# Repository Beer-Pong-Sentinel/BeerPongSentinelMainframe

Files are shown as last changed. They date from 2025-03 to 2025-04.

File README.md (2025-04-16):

# Beer Pong Sentinel Project
This page contains a detailed description of the Beer Pong Sentinel project for the Engineering Physics capstone course at UBC.

## Our Team

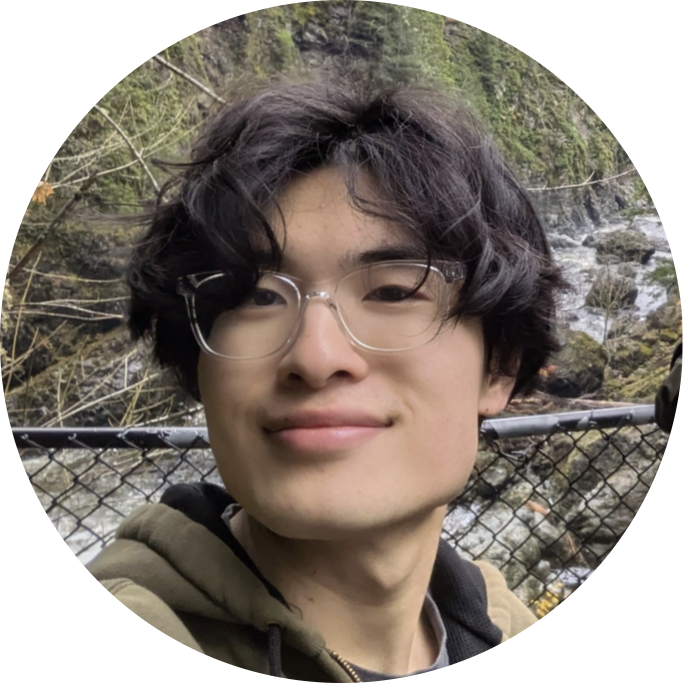
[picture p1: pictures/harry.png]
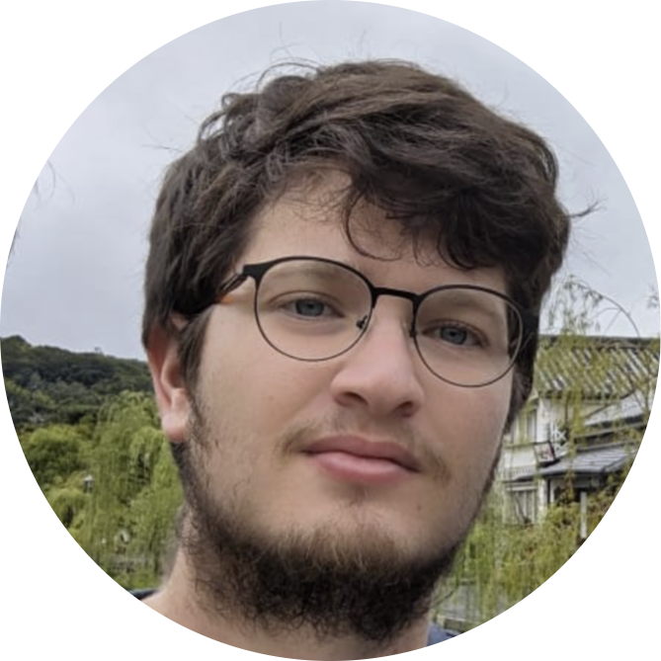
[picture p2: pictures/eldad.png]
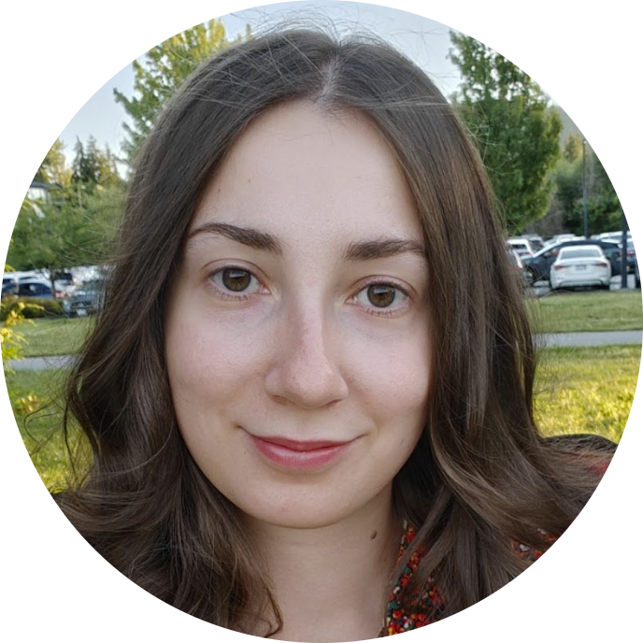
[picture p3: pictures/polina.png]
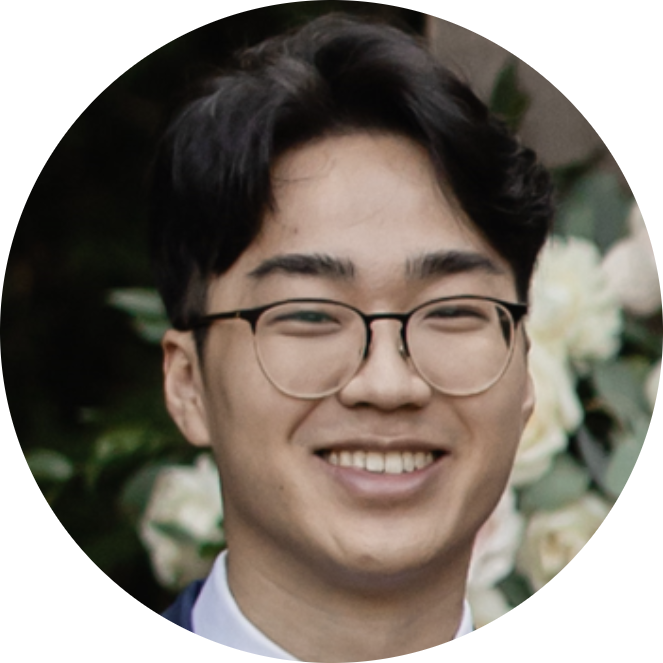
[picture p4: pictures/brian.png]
|  |  |  |  |
|:---:|:---:|:---:|:---:|
| **Harry Hu** | **Eldad Zipori** | **Polina Shopina** | **Brian Yan** |
| [LinkedIn](https://www.linkedin.com/in/harrytyhu/) | [LinkedIn](https://www.linkedin.com/in/eldad-zipori-a411a5157/) | [LinkedIn](https://www.linkedin.com/in/polina-shopina/) | [LinkedIn](https://www.linkedin.com/in/brian-yan/) |

## Background
The inspiration for this project came from an innocent university game - beer pong.
We thought, “it would be pretty cool to build a robot that could intercept all of our opponent's shots”! 

Although we've pivoted away from ping pong balls to the larger and more predictable tennis balls, our goal remains the same: to prevent a target from reaching a zone at the edge of a table using an interception system.

### General Interception Process
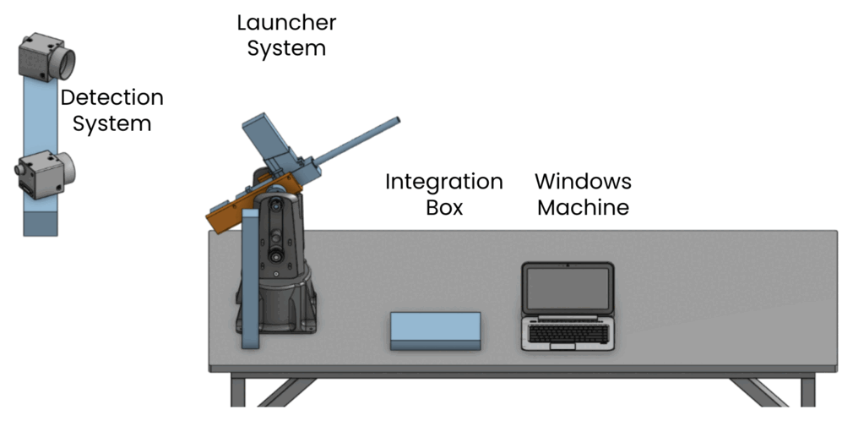
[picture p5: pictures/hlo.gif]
High Level Overview


The small animation shows the different high level stages our system has to take to intercept a ball.

First you see the general setup of our system, and it's different components. The remaining steps are as follows:
* our cameras detect a tennis ball in the air and triangulate its 3D location
* our cameras continue capturing frames until we have enough data to predict the target's trajectory
* we compute the predicted trajectory and based on our understanding of system latency, determine where along the trajectory to intercept the target
* we rotate our launcher in the altitude and azimuth directions
* we trigger the launcher to fire an interceptor at the right time

### Error, Latency, Jitter, and Uncertainty

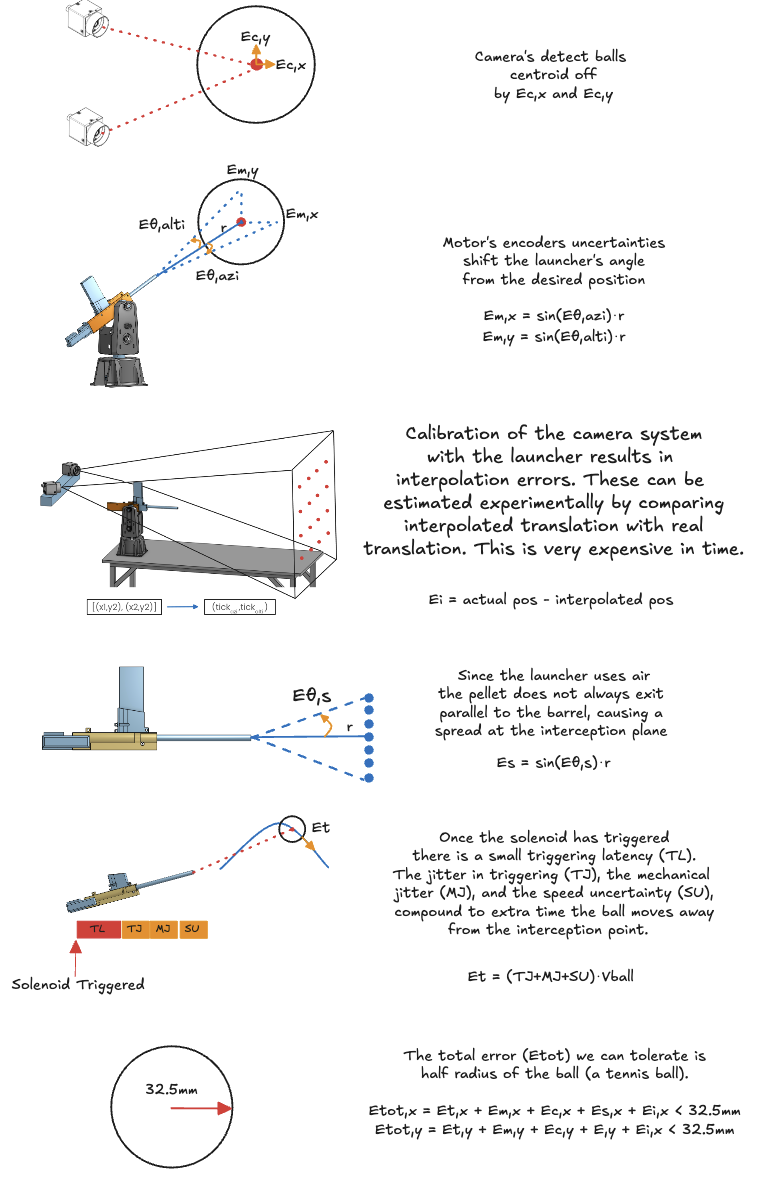
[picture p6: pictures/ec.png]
Error Diagram


The last error we need to account for is the error in the prediction itself. This comes from the differences in actual ball trajectories vs the trajectory we predict for them. To measure this simply compare  a trajectory of a ball from a video, to a predicted trajectory. Most of the work on this is done and can be found in (...).

Our estimates for all the errors are provided in the table below.
|Source| Symbol | Quantity | Units |Notes|
|---|---|---|---|---|
|Prediction|Ep|N/A||Need to collect data|
|Integration|Ei|N/A||Need to collect data|
|Cameras|Ec|0.3-0.8|Pixels|Result of camera's triangulation|
|Motors - Azimuth|Eθ,azi|0.450|Degrees| Manufacturer data|
|Motors - Altitude|Eθ,alti|0.057|Degrees|Manufacturer data|
|Pneumatic Mechanism| Eθ,s|0.00485| Radians | Maximum measured spread|
|Electromechanical Jitter| Et|1.2|milliseconds| Maximum measured jitter| 

_Note_: The integration error Ei encapsulates the error in the cameras and the motors when trying to aim at a target after motor-calibration. It can be thought of as the shortest distance between a laser beam collinear with the launch barrel and a stationary target's centroid.

_Note_: Some values such as the integration error Ei are not calculated yet. Prediction is only theoretical as we did not fully integrate it. 

<!-- _Why have different units?_\
We would like to get the most accurate estimation for the maximum error in our system. For that reason we comply with the manufacturer choice of unit, and covert the units only when plugging into the final error estimation.  -->

<!-- _Note_: We are assuming the pallet travels at around the speed the manufacturer claims *131meters per seconds*. -->

### Interception Timeline
To truly understand this project you will need to understand the timeline in which the system operate. This might take a few seconds (or a few months).

The important thing to note here that prediction is implemented assuming worst-case latency for all processes. This means that the only jitter that affects our interception error is the electromechanical jitter in our triggering mechanism as we always wait a constant amount of time before firing.

<!-- Since the launcher provide a move done command, we recommend to always choose an interception point as if all jitter before the move done actually happens, this will cause the error in interception to come only from actions taken after the move done status (plus the error from the LUT itself.).

This makes the main challenge problem of interception the timing of the triggering itself. This is since all error's are measureable.  -->
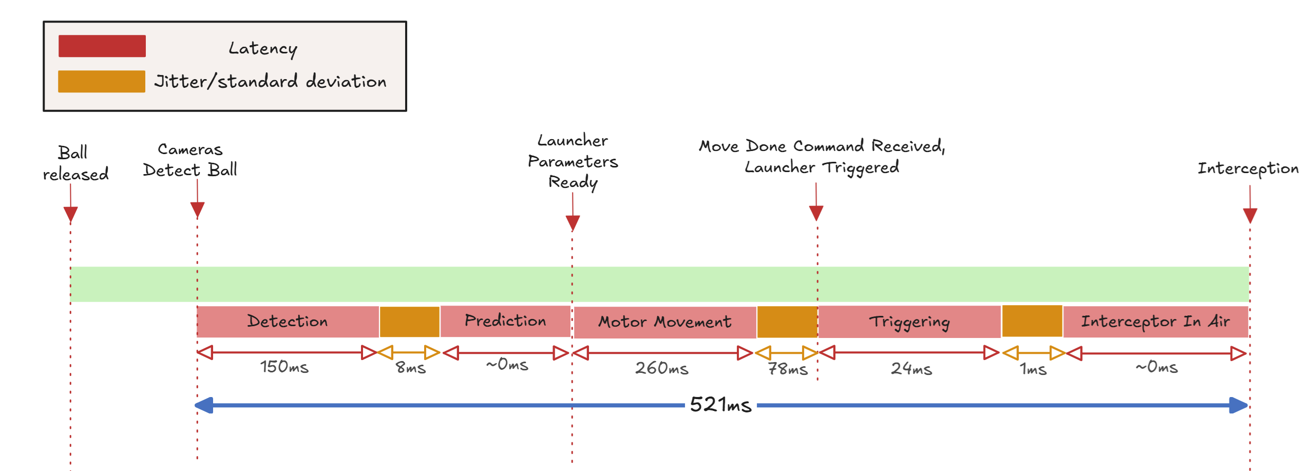
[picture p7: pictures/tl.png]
Interception Timeline


## Electrical
### Layout
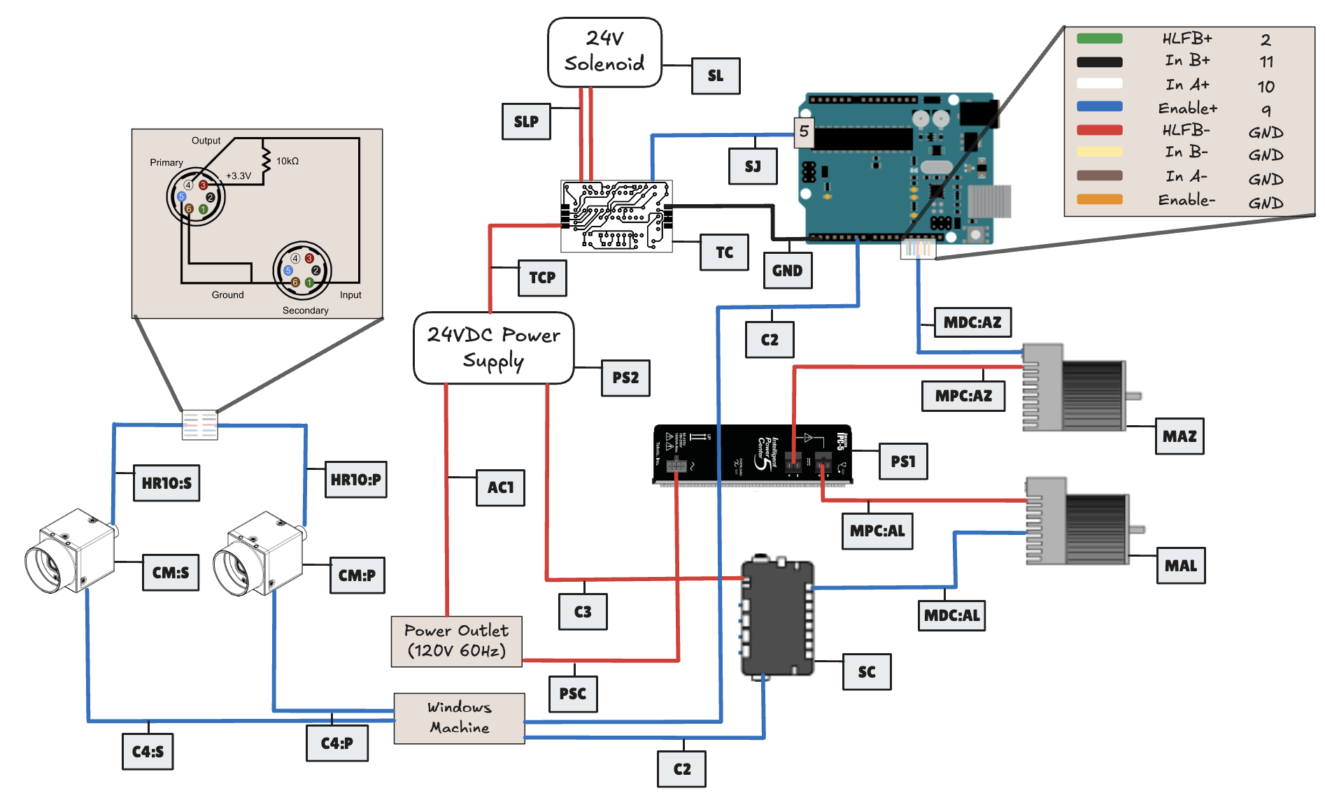
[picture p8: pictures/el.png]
Electrical Layout Electrical Components Layout


### Components
|Designation| Description | Part Number | Amount | Datasheet |
|---|---|---|---|---|
|CM| Blackfly S Camera | BFS-U3-04S2C-C  | 2 |[Teledyne](https://www.teledynevisionsolutions.com/products/blackfly-s-usb3/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)|
|MAZ| Stepper Motor | CPM-SDSK-3421S-RLN  | 1 |[Teknic](https://teknic.com/model-info/CPM-SDSK-3421S-RLN/?model_voltage=48VDC)|
|MAL|SDK Motor | CPM-SCSK-3411S-ELNB  | 1 |[Teknic](https://teknic.com/model-info/CPM-SCSK-3411S-ELNB/?model_voltage=75) |
|PS1| Motor Power Supply | IPC-5 | 1 | [Teknic](https://teknic.com/products/servo-motor-dc-power-supply/)|
|PS2| 24VDC Power Supply | SE-450-24 | 1 |[Mouser](https://www.mouser.ca/ProductDetail/MEAN-WELL/SE-450-24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)|
|SC| Motor Control Hub | SC4-HUB  | 1 |[Teknic](https://teknic.com/sc4-hub/) |
|SL| 12V Solenoid 42N | 10MM JF-1253B | 1 |[ Lee's Electronics](https://leeselectronic.com/en/product/4408-12v-solenoid-42n-10mm-jf-1253b.html) |
|TC - N/A| Voltage regulator | LM7805 | 1  | [Texas Instruments](https://www.ti.com/lit/ds/symlink/lm340.pdf) |
|TC - D2| Diode | 1N4007 | 1 | [Vishay](https://www.vishay.com/docs/88503/1n4001.pdf) |
|TC - Q1| MOSFET | IRF540 | 1 | [Vishay](https://www.vishay.com/docs/91021/irf540.pdf) |
|TC - Q2/Q3| BJT | 2N3904 | 2 | [Onsemi](https://www.onsemi.com/download/data-sheet/pdf/2n3903-d.pdf) |

### Connections
| Designation | Description | Part Number  | Amount | Link|
|---|---|---|---|---|
| MPC | Motors Power Cable | CPM-CABLE-PWR-MS120  | 2 | [Teknic](https://teknic.com/cpm-cable-pwr-ms120/) |
| MDC | Motors Data Cable | CPM-CABLE-CTRL-MU120  | 2 | [Teknic](https://teknic.com/CPM-CABLE-CTRL-MU120/) |
|PSC| Power Supply Cable| IPC35-CABLE110 | 1 |[Teknic](https://teknic.com/ipc35-cable110/)|
|HR10| Camera GPIO Cable| HR10A-7P-6S | 1 |[Teledyne](https://www.teledynevisionsolutions.com/products/hirose-hr10-6-pin-circular-connector/)|
|C1| USB-A to USB-B|  | 2 ||
|C2| Micro USB to USB-B/C|  | 2 ||
|C3| 2-pin Molex to Ring Connector | |2||
|C4| USB3 to Micro-B | |2||
|SJ| Jumber Wire|  | 2| | 

### Solenoid Control Circuit
_Note:_ The physical circuit in the current setup of the project is not the printed PCB, but a breadboard version without the option for a manual control and a 5V voltage regulator that steps down the 24V for the solenoid.

The full KiCAD design for the solenoid control PCB can be found inside `sol_ctrl_pcb`.
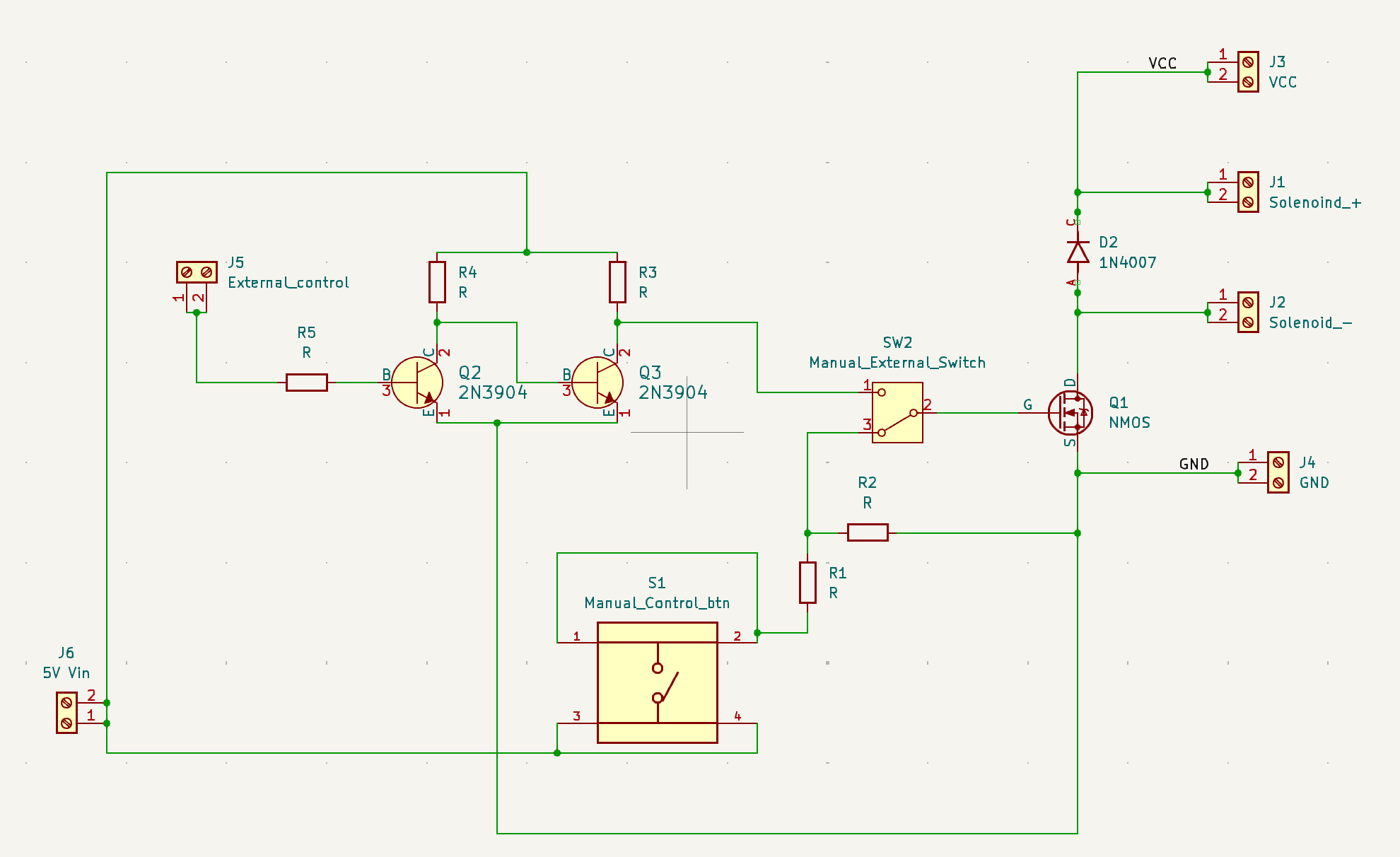
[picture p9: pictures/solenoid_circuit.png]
Proposed Solenoid Circuit

## Mechanical 
 
The original BB gun we got for this project is the [Crosman R1 Full-Auto - Black](https://www.crosman.com/product/crosman-full-auto-r1-black-bb/).\
The pneumatic mechanism requires two [12-gram Powerlet CO2 Cartridges](https://www.crosman.com/product/crosman-12-gram-powerlet-co2-cartridges/).\
This magazine uses [4.5mm copper pellets](https://www.crosman.com/product/crosman-copperhead-bbs/).

### Safety

When testing or operating the BB gun pneumatic mechanism/especially in a closed room, make sure to wear face protection. The pellets are copper and tend to bounce around. This will happen after a while even if you have a cardboard stack target. 

*To learn more about safety and replacing gas cartridges:* head to the `safety` folder and read about safety of operating the BB gun in testing locations and how to safely replace the gas cartridges for the pneumatic mechanism. 

### Launcher Modifications
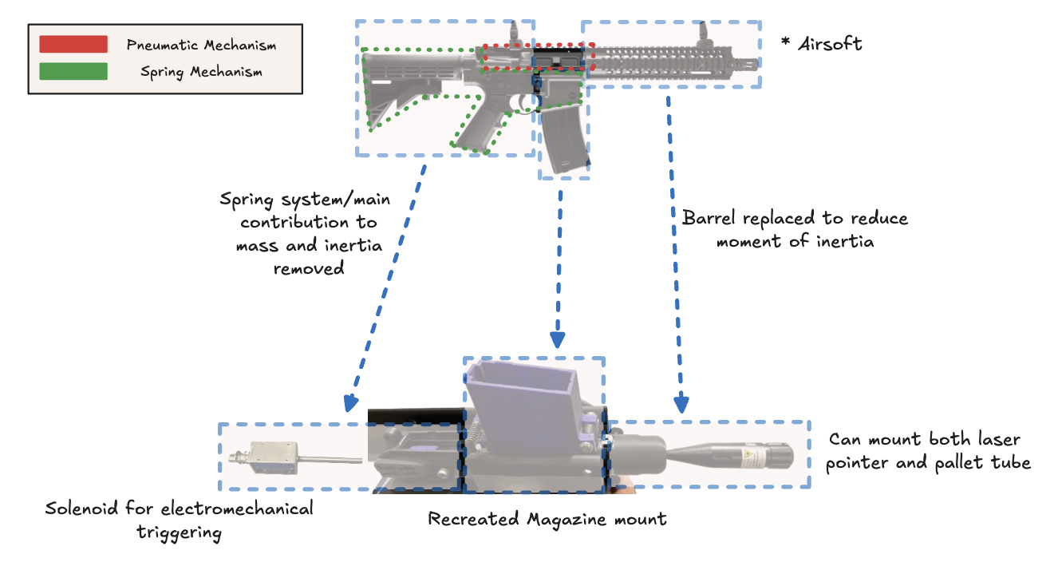
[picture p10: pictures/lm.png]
Launcher Modifications


The main rational behind modifying the original BB gun is to reduce the mass, size, and moment of inertia to allow up to actuate our launcher with ease. A larger, weirdly shaped, launcher would have required much more expensive motors and a more rigid design for the launcher mounts. 

### Launcher's Moment of Inertia
Calculating the moment of inertia for the launcher plays a key role in the design and motor selection.

The below figure shows our CAD model of the launcher with its mechanical parameters. The marker/arrows indicate the mounting location for the launcher.

The launcher's model was built by weighting its various components and recreating the rough or exact shapes of its components. The result parameter should be considered as a lower bound. We recommend using a factor of safety of 1.5 at least in any calculations that include these parameters.

[Onshape link for the launcher model](https://cad.onshape.com/documents/76652a767c23fe435988178b/w/9803612b38e4d7d0dd289d8c/e/d43adc66a7cc15ee7d39c4dd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)

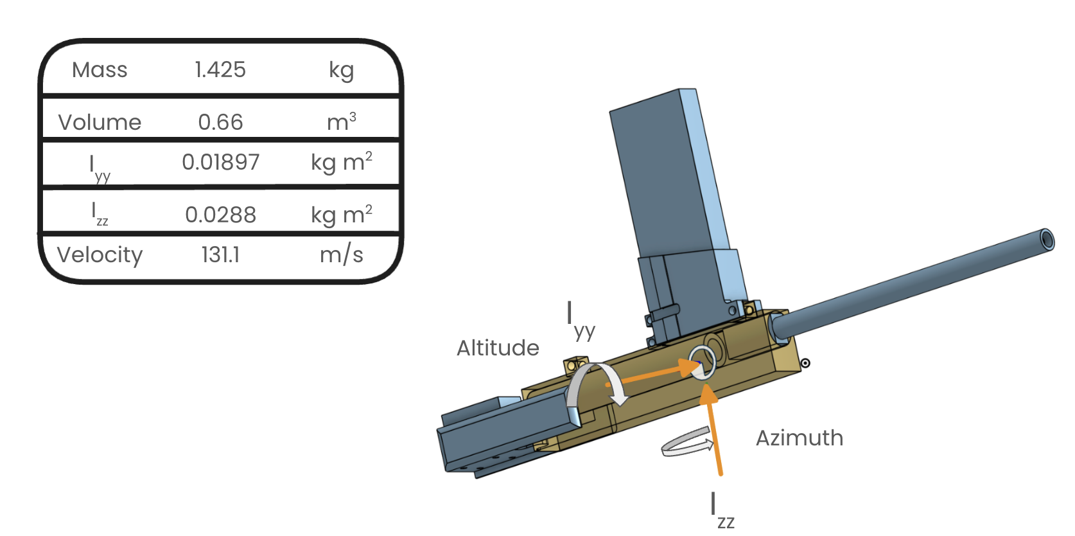
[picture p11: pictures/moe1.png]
launcher and Moment of Inertia


### Motor Selection
To select motors we ran simulations of motion profiles using both the inertia of our launcher and the rotor inertia of some promising motors. 
We simulate both a triangular motion profile, which assumes instant change from acceleration to de-acceleration, and a trapezoidal motion profile, which assumes equal time in acceleration, operation in max acceleration, and deceleration. 

<!-- While both are not perfect and can be improved, by giving assuming less time in max acceleration for example, they give us a good idea of the torque and velocities we will need to operate in to actuate our launcher.  -->

The model takes the following parameters:
```python
object_inertia 
motor_inertia 
theta_target 
time_window
safety_factor
```

We recommend being conservative with the safety factor to account for imperfections in tuning, inertia calculations, and motion profile control.
An example of such triangular motion profile can be seen below. 

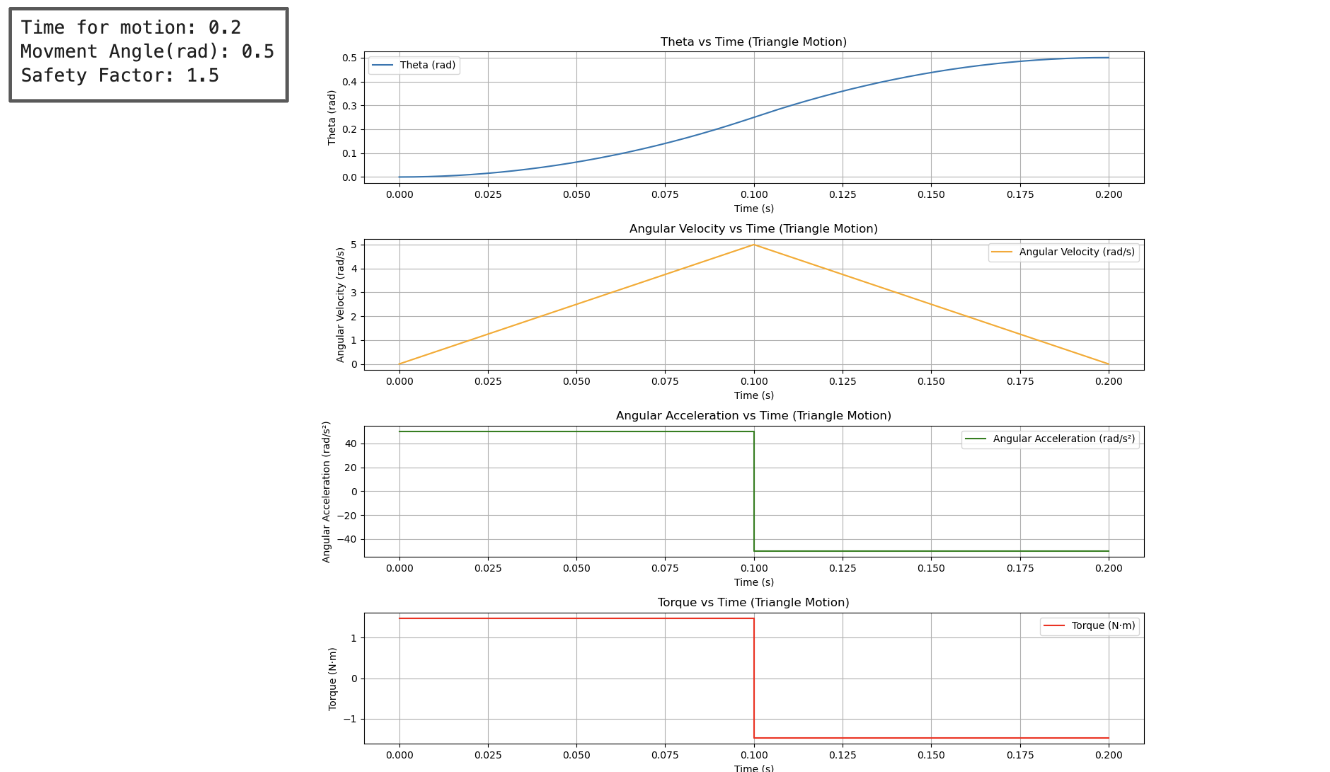
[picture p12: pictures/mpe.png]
Motion profile Example


_Note_:\
Something we learned in the hard way is that the rotor inertia should match the inertia of the load it drives. This mostly affects tuning the motor. In the case it does not match, you might want to gear the motor. This is not ideal as it will cause a loss in resolution of the encoder, but will provide better tuning. 

_Our problem_:\
Specifically with the motors we are using we found out that our altitude motor (SDK controlled) does not allow to limit the velocity for tuning. This causes the motor to saturate in torque and to produce sub-optimal tuning. To mitigate this, we created a program in our software to map the time it take to move to an angle with a certain velocity limit. Creating a map of `(velocity, angle)` to `(time taken)`. We can use this to find the optimal maximum velocity to use to minimize the time it takes to go to any given angle. 

These profiles can be ran for any internal parameters you can change in the motor. We only found that you can change the Jerk and the "Fine-tuning" (how stiff/quite the motor moves) in our altitude (SDK controlled) motor. 

Such motion profiles with different jerk control settings are shown below (the graphing script can be found at [./motors/Altitude Time Motion Profile Visualization.ipynb](https://github.com/Beer-Pong-Sentinel/BeerPongSentinelMainframe/blob/main/motors/Altitude%20Time%20Motion%20Profile%20Visualization.ipynb)). 

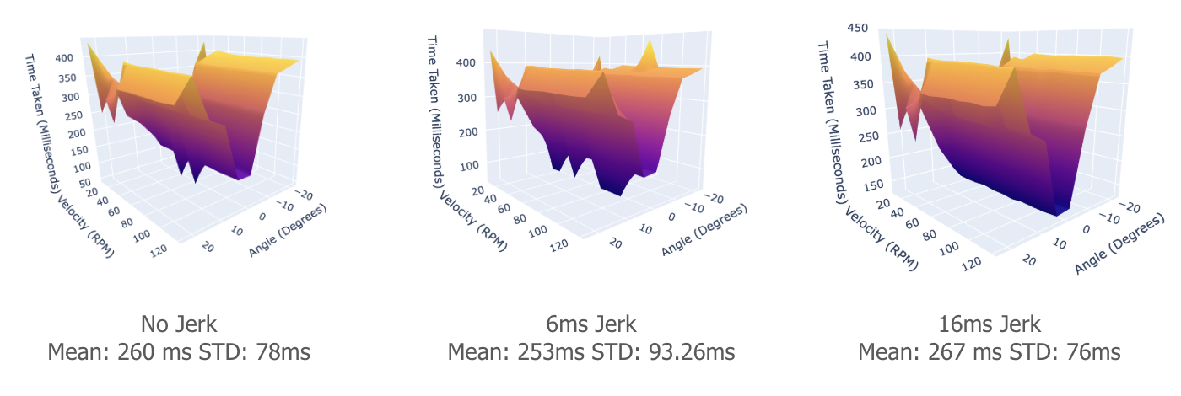
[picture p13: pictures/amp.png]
Altitude Motion Profiles


From this analysis, we determined that using no jerk control and a velocity limit of 20 RPM produces the optimal jerk and latency over our range of possible altitude angles.

### Motor Tuning
Both motors need to to be tuned with ClearPath (azimuth) and ClearView (altitude). The tuning we are using can be found under the [./motors](https://github.com/Beer-Pong-Sentinel/BeerPongSentinelMainframe/tree/main/motors) folder with the timestamp and description.

_Important Last Minute Note:_ We found out that the calibration files are readable! That means that you can tune the motor by changing their parameters. A sub-project for this will be to make your own tuning program that will limit the velocity of the altitude motor and tune it well (though this is more Teknic's job).
### Components

| Description | Part Number  | Amount | Link|
|---|---|---|---|
| Timing Belt Pulley 1.500" OD, for 1/2" Shaft Diameter | 6495K752  | 2 | [McMaster](https://www.mcmaster.com/6495K752/) |
| Rotary Shaft 1/2" Diameter, 6" Long | 4149N15  | 1 | [McMaster](https://www.mcmaster.com/4149N15/) |
| Ball Bearing for 1/2" Shaft Diameter |60355K173| 3 |[McMaster](https://www.mcmaster.com/60355K173/)|
| Series Timing Belt| 6484K226 | 1 |[McMaster](https://www.mcmaster.com/6484K226/)|
|  Dry-Running Nylon Sleeve Bearing Flanged, for 1/2" Shaft Diameter and 3/4" Housing ID, 7/16" Long| 6389K233 | 2 |[McMaster](https://www.mcmaster.com/6389K233/)|
| Carbon Steel Wide-Rim Ring, 0.048" Thick x 1/2" ID x 7/8" OD| 97669A200 | 1 (pack of 25) |[McMaster](https://www.mcmaster.com/6389K233/)|

### Launcher Mount and Maneuvering
_Click to open OnShape CAD model_
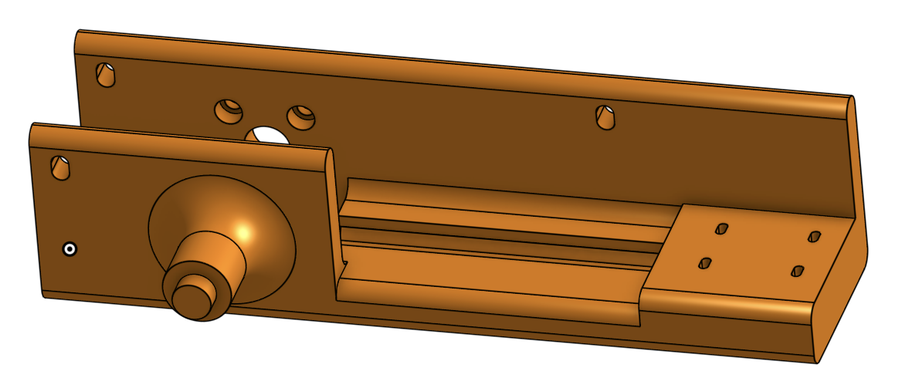
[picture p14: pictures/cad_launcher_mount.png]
Launcher Mount (https://cad.onshape.com/documents/360e54d875f63ab4db6ef54b/w/d57eff492a0fd340cef803da/e/a90c483078f0a216147ba77b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)
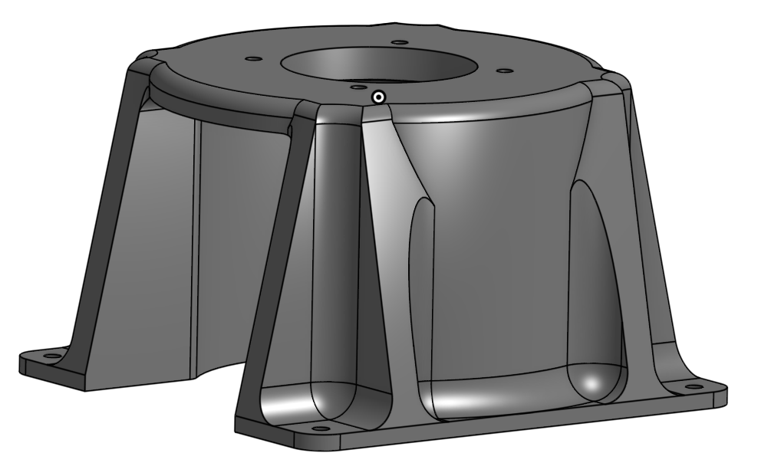
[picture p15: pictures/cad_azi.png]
Azimuth Mount (https://cad.onshape.com/documents/360e54d875f63ab4db6ef54b/w/d57eff492a0fd340cef803da/e/af73ce29d204dcf42df93766)
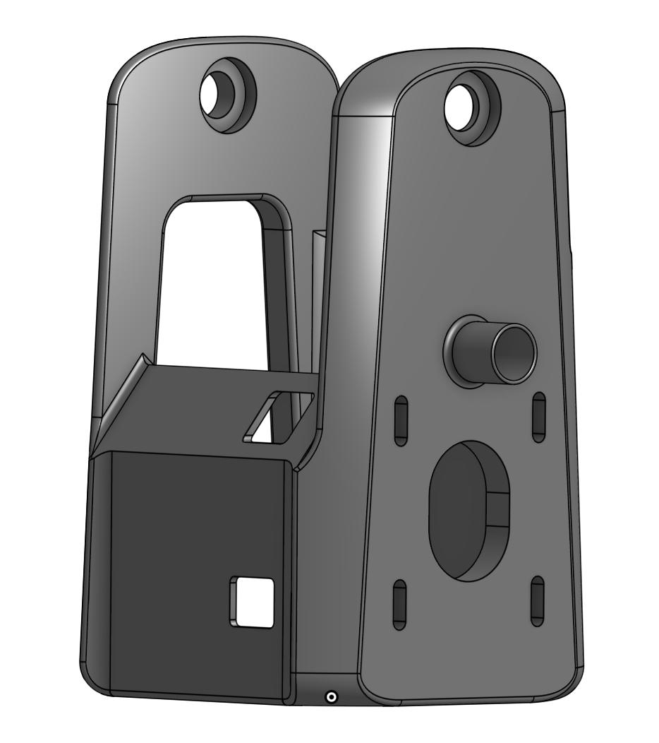
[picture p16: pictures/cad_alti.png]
Altitude Mount (https://cad.onshape.com/documents/360e54d875f63ab4db6ef54b/w/d57eff492a0fd340cef803da/e/c06067e56aa459f53e365584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)
|  | | |
|---|---|---|
### Assembly 

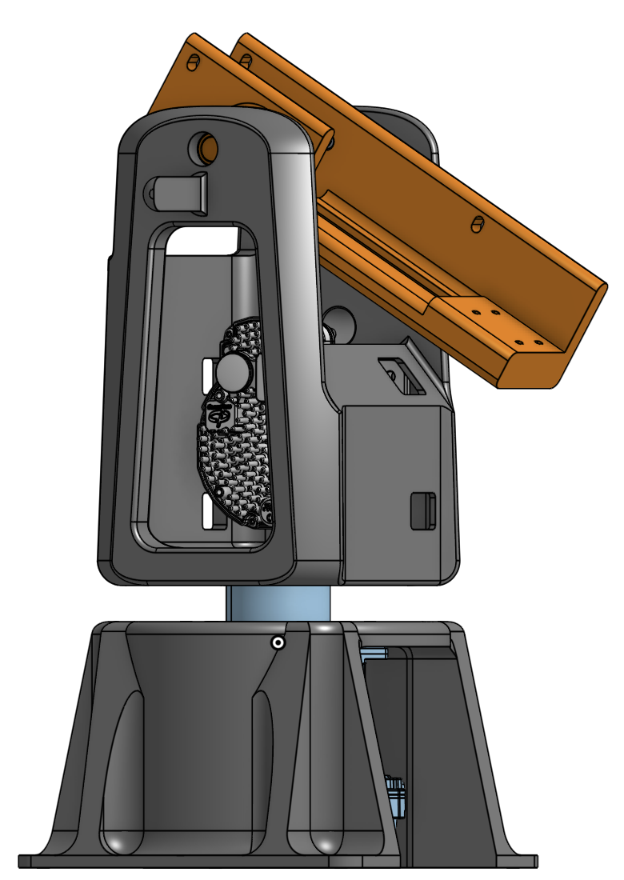
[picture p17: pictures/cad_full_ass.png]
Full Assembly (https://cad.onshape.com/documents/360e54d875f63ab4db6ef54b/w/d57eff492a0fd340cef803da/e/76fc739196417cc4943c6696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)


## Firmware
The full firmware project can be found in the `firmware` folder. Our firmware runs on an Arduino Uno with the following pins connected. 

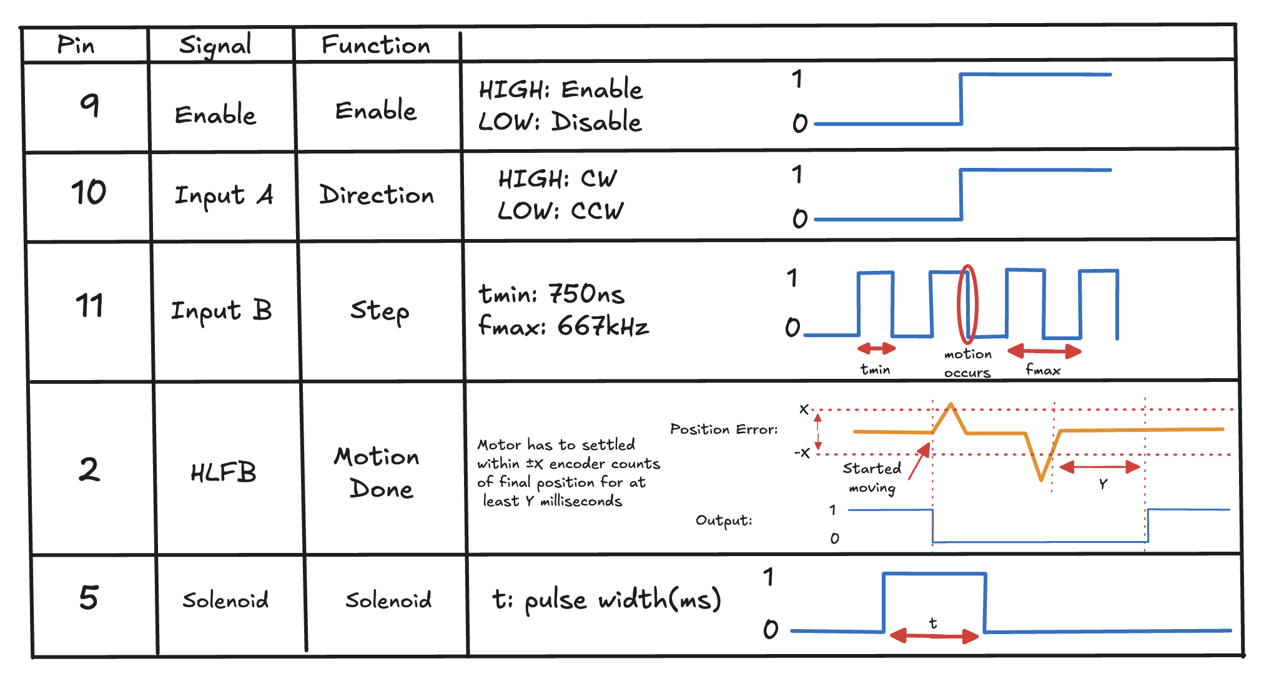
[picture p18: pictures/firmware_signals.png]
Firmware's Parameters


### Firmware Parameters
**_Solenoid Pulse Width:_**\
Location: firmware\
Variable: TRIGGERING_DELAY\
Scale: Miliseconds\
Current Settings: 75\
Considerations: 
- Time needs to be enough to allow for the solenoid to provide enough force to open the CO2 valve.
- Time should be too long as it wastes CO2.

**_Step Signal Pulse Width:_**\
Location: firmware\
Variable: AZI_DELAY\
Scale: Microseconds\
Current Settings: 100\
Considerations: 
- Minimum specification of motor control must be met
- Rise/fall time affect on the pulse
- Motor minimum control voltage is 5V
- Effect on motion profile; how steps in certain frequencies translate to different velocities

_Note:_ Currently this sets both the pulse width and the frequency of pulses as the high time and low time are symmetric. This can be changed.

**_Azimuth Motor Settlement Range:_**\
Location: ClearPath MSP\
Access: Advanced -> High-Level Feedback (HLFB) Setup -> In-Range Position Window (ctns)\
Current Settings: 1\
Notes: Current HLFB Output setting is All System Go (ASG) - Position\
Considerations: 
- Azimuth motor has a smaller encoder resolution than altitude
- See altitude considerations

**_Azimuth Motor Settlement Delay:_**\
Location: ClearPath MSP\
Access: Advanced -> High-Level Feedback (HLFB) Setup -> Verify Time (ms)\
Current Settings: 10.1\
Notes: Current HLFB Output setting is All System Go (ASG) - Position\
Considerations: 
- Azimuth motor tuning runs better the altitute
- See altitude considerations

**_Altitude Motor Settlement Range:_**\
Location: ClearView\
Access: Details -> Move Status Indicators... -> In-Range Position Window (ctns)\
Current Settings: 5\
Considerations:
- We have some tolerance for error so we can settle within some range of the encoder ctns
- Moving faster might take priority.

**_Altitude Motor Settlement Delay:_**\
Location: ClearView 
Access: Details -> Move Status Indicators... -> Verify Time (msec)\
Current Settings: 10.1\
Considerations:
- Move done might given more than once if the launcher oscillates around a point.
- More delay means more latency before we can trigger.

## Camera system

### Camera's Parameters
The full camera parameters can be found under `/simulations` and `data analysis/Camera Calculations.xlsx`.
This provides the full details of all the intrinsic parameters of the [BFS-U3-04S2C-C]((https://www.teledynevisionsolutions.com/products/blackfly-s-usb3/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)) cameras we are using, inluding some that require calculations. 

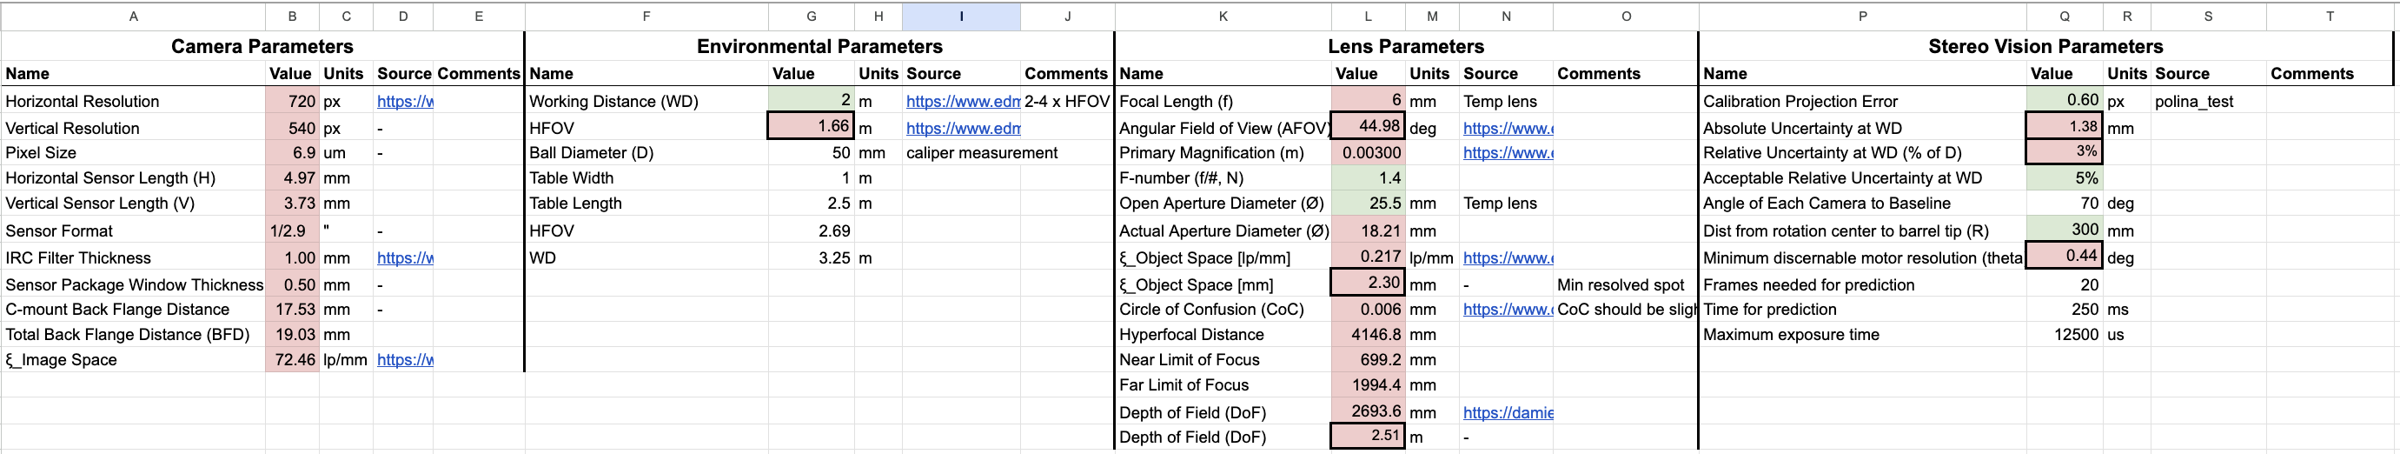
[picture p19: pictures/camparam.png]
Camera's Parameters Table


### Intrinsic/Extrinsic Calibration 
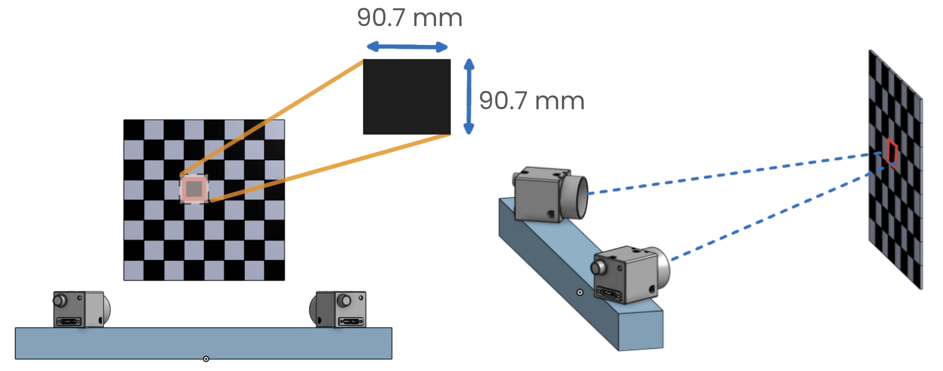
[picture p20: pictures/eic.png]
Chessboard Setup


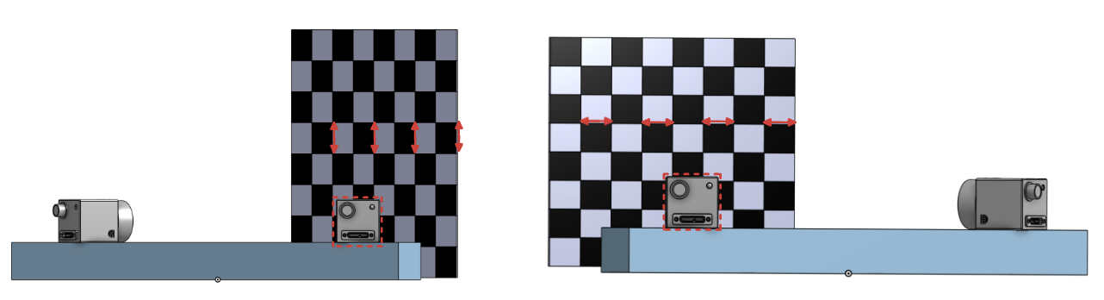
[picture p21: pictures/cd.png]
Camera's Distortion

We use stereo calibration to to correct for lens distortions and determine the precise relative placement of two cameras. We use a printed chessboard pattern of known dimensions and take images at various positions and orientations. By analyzing these images, the calibration algorithm uses the known geometry of the chessboard to first estimate and correct each camera’s intrinsic parameters, “undistorting” the images. It then compares corresponding points in both camera views to determine the cameras’ relative positions and orientations. These calibration results, which include both the intrinsic corrections and the extrinsic parameters describing how the cameras are arranged, can be combined into a projection matrix that enables the reconstruction of a 3D point using an image from each camera.

You can find some calibration data under [./calibration data](https://github.com/Beer-Pong-Sentinel/BeerPongSentinelMainframe/tree/main/clibration data) . As long as the orientation of the two cameras with respect to each other does not change you might not need to re-calibrate. Note that under most new environments it is recommended to recalibrate.
### Color Detection
Initially we tried to detect a static target (tennis ball) using conventional methods such as HSV/RGB thresholding. 
This turned out to be more challenging than we thought, as the camera resolution is only 720x540.

While colors seem green, or red, to us, it is very clear in processing that a tennis ball contains a lot of non-green content. 
To fix this we tried a few things:
- Putting a black curtain in the background to more easily see the green tennis ball
- Increasing the saturation on the cameras making most of the view look red, but making green more clear to distinguish
- We used clear, consistent lighting that does not flicker and turned off all the other light sources in the room.

In order to intercept the ball at some point along its trajectory, we need to triangulate its position across 3D space both quickly and accurately. However, to triangulate the position of the ball, we need to determine the pixel coordinates of the center of the ball for each image from our two cameras. Thus, we need a robust image processing pipeline that can efficiently and consistently retrieve the centroid of a ball from an image.

We constructed the Ball Detection pipeline to accomplish this task which works as follows:

1. First, apply an HSV threshold to the image, which highlights only objects within a certain hue, saturation, and value range. 
2. Next, apply a MOG2 background subtraction to identify any moving objects in the image. 
3. Combine these two outputs in order to retrieve only moving objects which match the specified colors defined by the HSV range. 
4. Once combined, apply a dilation and erosion process to remove any noise. The final image should contain only highlighted pixels that match the position of the ball.
5. Lastly, find the centroid of the highlighted pixels for both camera's and pass these values to the triangulation function to determine the position of the ball in 3D space.

To read more about HSV and RGB thresholding, see [OpenCV's official documentation](https://docs.opencv.org/3.4/da/d97/tutorial_threshold_inRange.html).

### Yolo-OpenCV Object Detection 
Eventually, we decided to use a deep neural network (DNN) for static ball detection. While our final goal is prediction of a moving target, we require this to be able to demo our camera-launcher calibration, and to be able to give an estimation of its error.

YOLO is an open source model for object detection. It is extremely easy to use and has very impressive performance. We are using *YOLOv8*, for compatibility and reliability.

Read more about [YOLO in the official site](https://docs.ultralytics.com/).

To train our YOLO model we simply found [a dataset](https://universe.roboflow.com/alexa-wpmns/tennis-ball-obj-det/dataset/8) that looked promising to us and worked well when we tested it online.
We found a dataset with 4725 annotated images of tennis balls. 

<!-- The important part for this is that high precision, and the images were not only in a tennis court (which would probably not be so good for detecting a tennis ball in a general environment). -->

Training the model itself is straightforward and was done using a CLI.After training, we converted the trained model to ONNX format and loaded it into OpenCV’s DNN module, as C++ does not have a native YOLO library.\
[How to train a YOLO model](https://docs.ultralytics.com/modes/train/#usage-examples)\
[Read more about OpenCV DNN](https://docs.opencv.org/4.x/d2/d58/tutorial_table_of_content_dnn.html)

From this point onwards, we also wanted to utilize a dedicated GPU to do our image processing as fast as possible. For this we had to build OpenCV with CUDA nodes for DNN.\
[You can find how to build OpenCV and CUDA here](https://medium.com/@amosstaileyyoung/build-opencv-with-dnn-and-cuda-for-gpu-accelerated-face-detection-27a3cdc7e9ce)

### Cameras-Launcher calibration

To convert from a predicted point in 3D space to motor positions for interception, we require launcher-camera calibration. We accomplished this using a look-up table, which is created as follows. After placing a large surface in front of the launcher and attaching a laser pointer collinear with the barrel, we can move to a number of motor positions and record the 3D location of the laser dot on the surface. After repeating the process with the same motor positions and a surface further away from the launcher, we can connect the dots to obtain a vector and origin for each motor position. Because this becomes a lengthy process when collecting data for a fine grid, we can instead interpolate to approximate the vectors and origins we would see if we collected more data.

The process of converting from 3D coordinates to motor positions then becomes simple: we compute the distance between the desired 3D coordinate and each vector in the interpolated dataset. Then, we can simply read off the motor positions for the shortest distance. 

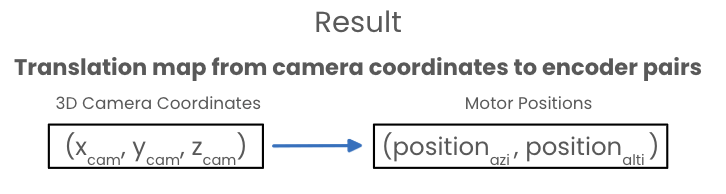
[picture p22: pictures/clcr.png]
Cameras Launcher Calibration Result


Ideally, the surfaces are placed such that the expected position of interception lies between them and that the angles swept over encompass all viable angles for interception. Having the surfaces further apart reduces uncertainty in the vector directions, although this means that surface size also has to increase. 

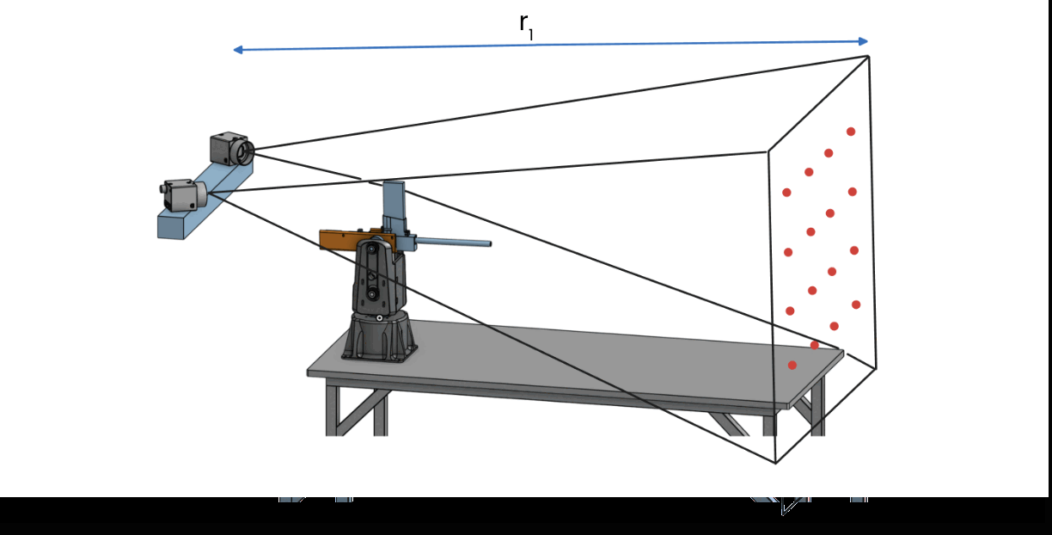
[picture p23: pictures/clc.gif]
Cameras Launcher Calibration


The main advantage of this method over others is that it does not assume much from the system (such as that the launcher has spherical symmetry, the surfaces are flat, etc.), making it robust. The main disadvantage is the time required to do such a calibration, which has to be redone whenever the position of the cameras changes relative to the launcher or each other.

We did not have the time to collect extensive test data for this approach but we found that collecting a 20x20 grid of data with altitude angles from 0 to 15 degrees and azimuth angles from -15 to 15 degrees, interpolated to 60x60 grid of data, we were able to measure an average error of 37 millimetres from the center of the target from initial tests.

You can find a full simulation for this calibration that was done prior to implementing it under [./simulations and data analysis/Laser_Cal_Sim.ipynb](https://github.com/Beer-Pong-Sentinel/BeerPongSentinelMainframe/blob/main/simulations%20and%20data%20analysis/Laser_Cal_Sim.ipynb) to see how we came up with this idea for calibration, including some estimations for the error it might have.

## Software - System Control and GUI
We developed a GUI using Qt in C++ to facilitate subsystem and integration testing.
The full project for the software can be found under [./system control gui](https://github.com/Beer-Pong-Sentinel/BeerPongSentinelMainframe/blob/main/system control gui).
### Dependencies 
- Qt 6.8.0 or 6.8.3 (we used [Qt Creator](https://www.qt.io/product/development-tools))
- [Spinnaker SDK](https://www.teledynevisionsolutions.com/products/spinnaker-sdk/)
- OpenCV Built with [Nvidia DNN](https://developer.nvidia.com/cudnn)
- [Teknic SDK](https://teknic.com/downloads/)
- [Eigen C++](https://eigen.tuxfamily.org/index.php?title=Main_Page)

### Programs
#### Motor Control
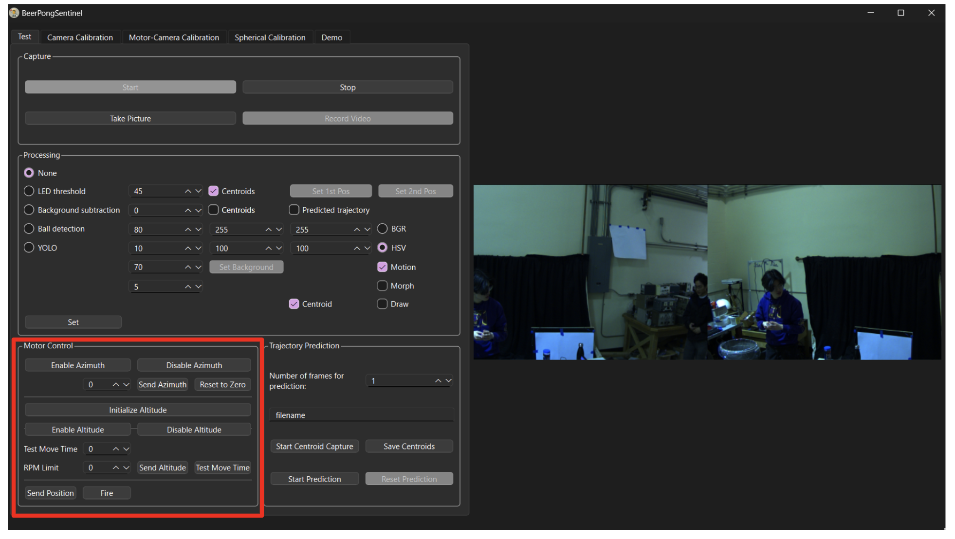
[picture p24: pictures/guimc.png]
Motor Control gui

This section provides a simple interface for enabling, moving, and disabling the azimuth and altitude motors. This allows to user to make sure both motors are properly connected. 

"Test Move Time" runs a script that iterates the altitude motor through a range of angles, repeating for a range of maximum velocities. The `(angle, velocity limit, time)` values are recorded in `altitude_time_test_dat.csv` within the Qt build folder.

#### Chessboard Calibration
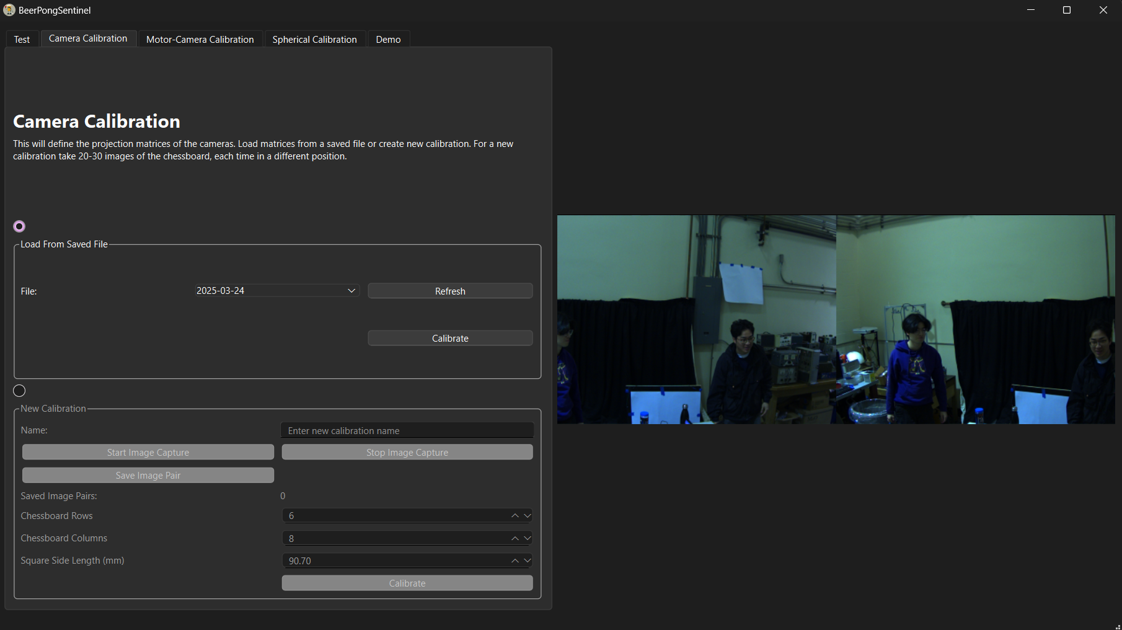
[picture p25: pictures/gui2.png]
Chessboard Calibration

This tab lets the user capture images to use for stereo calibration. We recommend taking 20-30 images where each corner of the chessboard is visible in both cameras. It is important that the camera feed on the left always corresponds to the camera physically on the left. If the cameras have not been moved relative to one another since another stereo calibration, the calibration can be loaded from a saved file.

#### Lookup Table Construction (Camera-Motor Calibration)
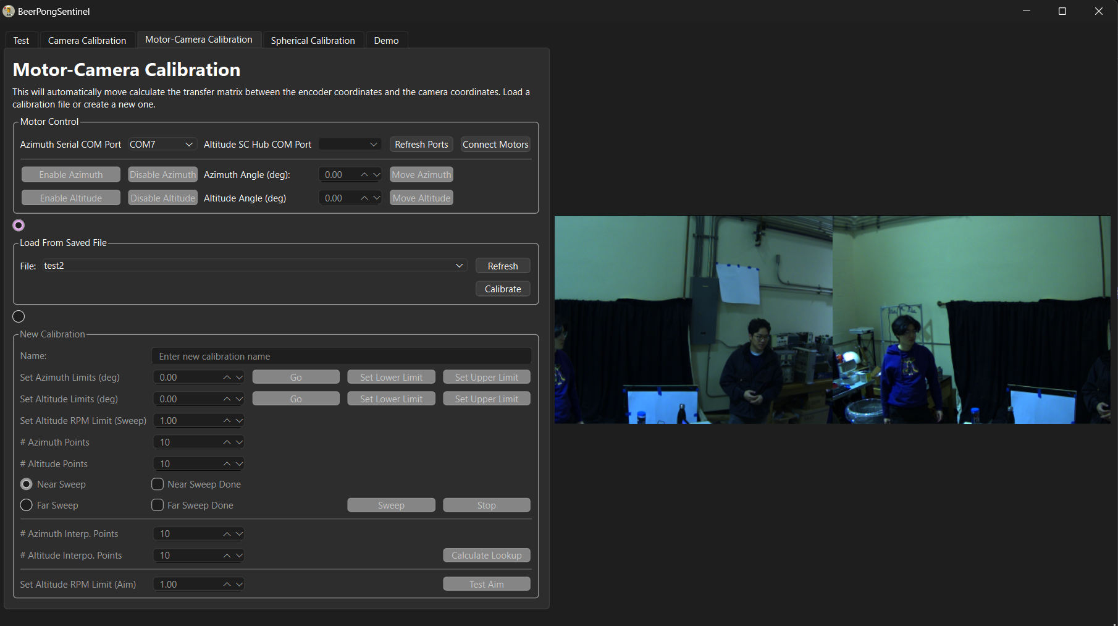
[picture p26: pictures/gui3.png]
Lookup Table Construction

This tab is used to generate a lookup table for camera-motor calibration. To do this, 
1. Select the correct ports for the azimuth and altitude motors.
2. Enable the motors and ensure that they can be moved.
3. Place a surface some some distance away from the launcher.
4. Insert a laser pointer collinear to the barrel.
5. Set the upper and lower azimuth and altitude angles such that the laser points to the edge of the surface at those angles.
6. With "Far Sweep" selected, press "Sweep", wait for the sweep to conclude, and check "Far Sweep Done".
7. Move the surface closer to the launcher, and repeat the process for the near sweep.
8. Press "Calculate Lookup" to generate the lookup table.

If the position of two cameras relative to each other and the launcher hasn't changed since the last calibration, the calibration can be loaded from a saved file.

#### Ball Detection (TODO)
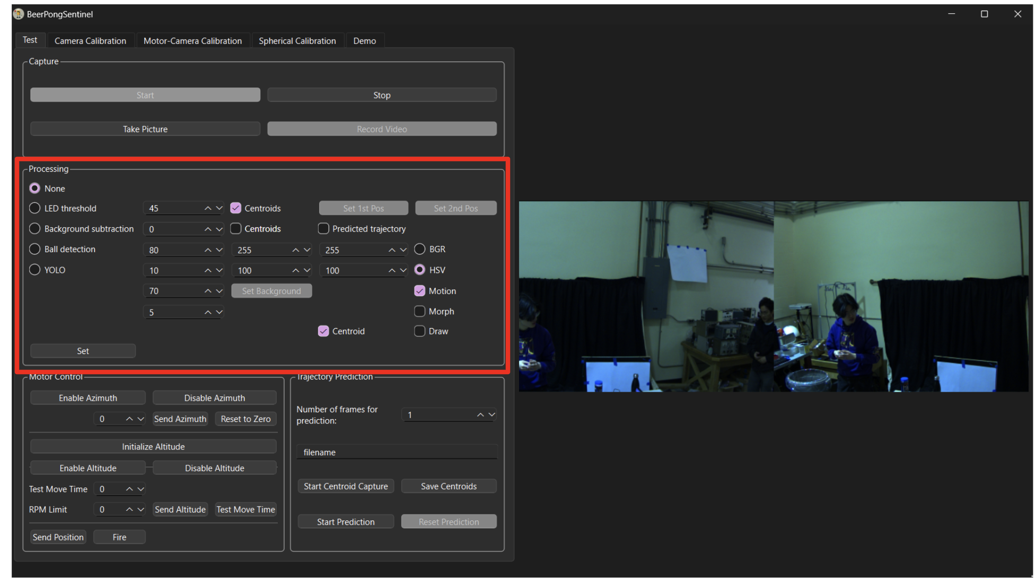
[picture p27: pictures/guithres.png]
Ball Detection


## Prediction
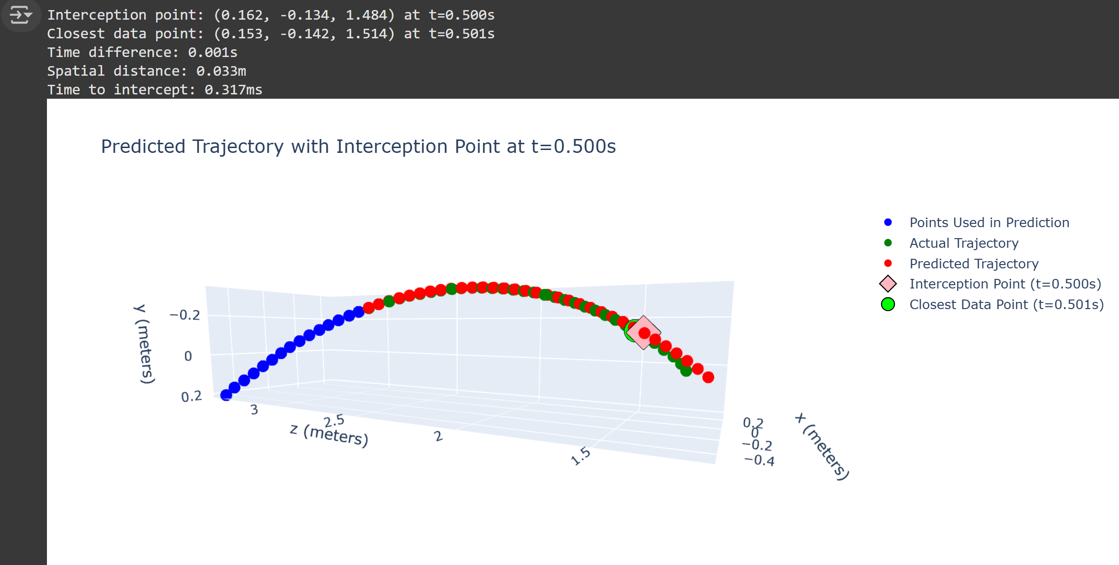
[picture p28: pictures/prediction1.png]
Prediction Example

Prediction is one of the central tasks of our project. We know our trajectory is going to be approximately parabolic, which allows us to use classical physics to create a prediction for the trajectory of the ball.

The full work for the different methods of prediction we test can be found under [./simulation and data analysis/PredictionSimulation.ipynb](https://github.com/Beer-Pong-Sentinel/BeerPongSentinelMainframe/tree/main/simulations%20and%20data%20analysis/PredictionSimulation.ipynb)
Under the [./simulation and data analysis/data](https://github.com/Beer-Pong-Sentinel/BeerPongSentinelMainframe/tree/main/simulations%20and%20data%20analysis/data) folder you can find data that we used for our trajectory simulation. This data can be extracted from our GUI.
We used real data we captured from our full camera setup in order to compare the predicted trajectory to a real life trajectory. 

### Gravity Calibration
To be able to predict accurately, we cannot just assume that gravity points down in our camera coordinates. To produce a gravity vector, we simply take a few videos with our camera system of us letting go off a ball. We then process this data to find the gravity vector, and to estimate the value that we are observing for gravity. This provides much more accurate results than just assuming gravity is 9.8 m/s.

The code we use to estimate the gravity vector can be found under [./simulations and data analysis/GravityEstimation.ipynb](https://github.com/Beer-Pong-Sentinel/BeerPongSentinelMainframe/tree/main/simulations%20and%20data%20analysis/GravityEstimation.ipynb).
## Our System In Real Life

### Launcher - Beerie
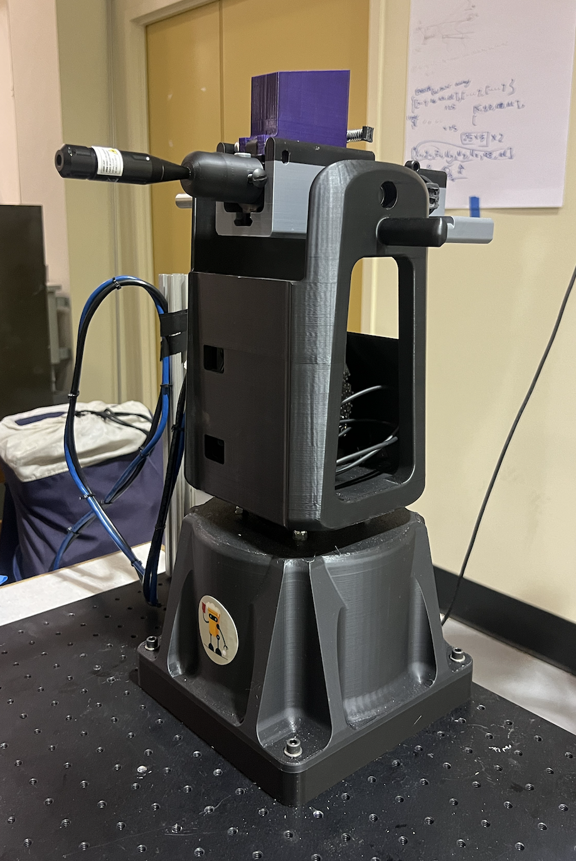
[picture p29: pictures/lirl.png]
Beerie


### Integration Box
Our full integrated circuitry connects all components together through a single hub USB hub for a simple connection.
Labels and markers, with detailed diagrams, make setting up quick and simple.
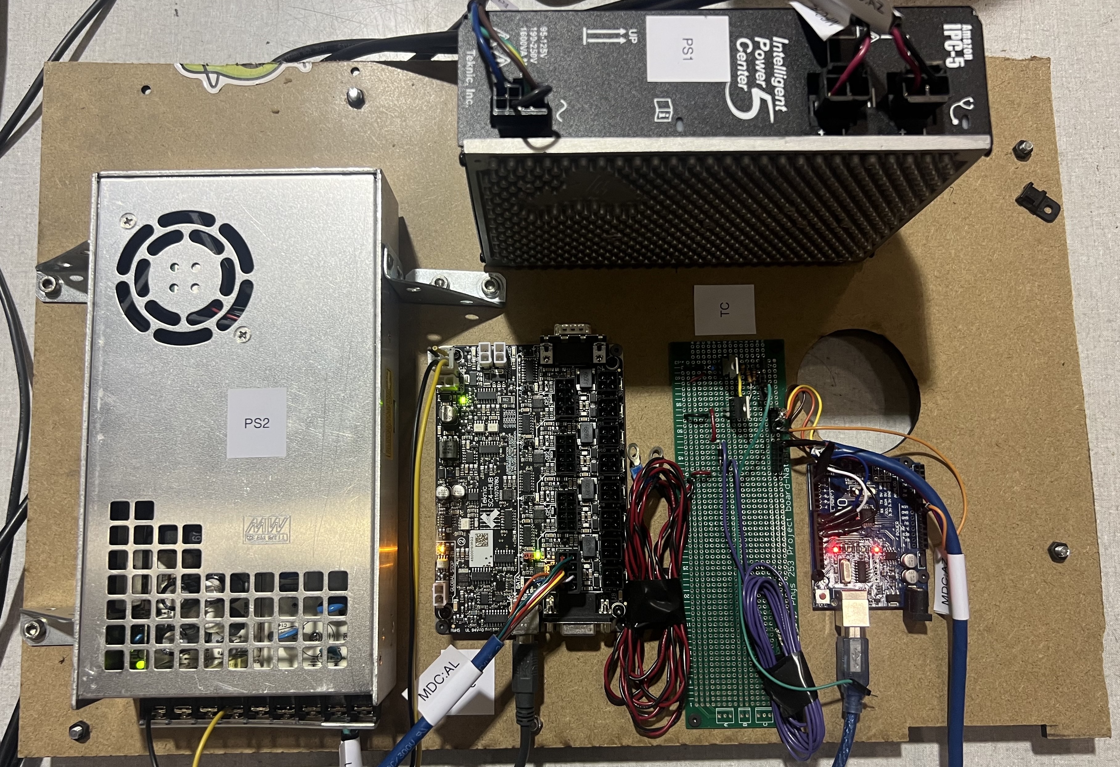
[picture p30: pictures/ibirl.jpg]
IRL Integration Box


### Cameras Setup
Our cameras are situated high with each 22.5 degree angle offset from their mounting point. This is done to capture a large range of view. We use high-power halogen lights to make sure the target is well lit at all times. These lights do not flicker which helps with background subtraction.
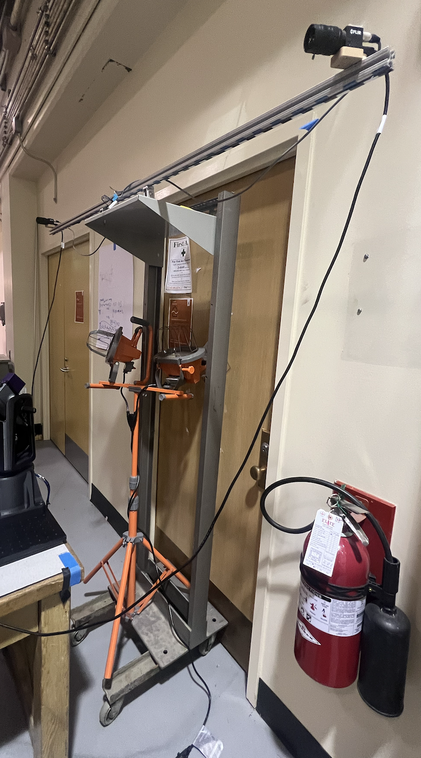
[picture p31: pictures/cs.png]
Cameras Setup


### Calibration Chessboard
Our 80cm x 60cm calibration chessboard is sandwiched between two acrylic plates, making it as flat as possible. 
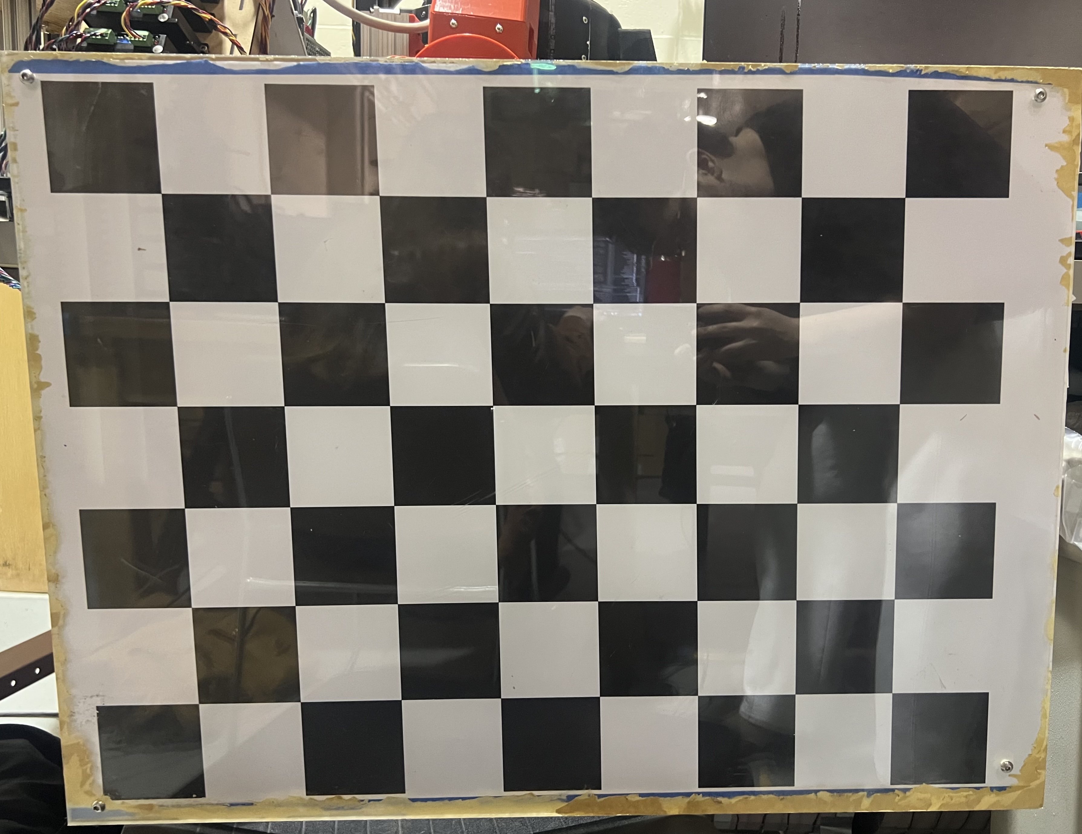
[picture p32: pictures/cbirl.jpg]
IRL Chessboard


### Aiming/Look up table calibration
Aiming Ball Perspective

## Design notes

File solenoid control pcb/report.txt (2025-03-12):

Warning: Width correction constrained.  The width correction value must be in the range of [0.000001 mm; 0.199999 mm] for the current design rules.
Plotted to '/Users/eldadzipori/Documents/Solenoid Control/Solenoid Control-F_Cu.gbr'.
Plotted to '/Users/eldadzipori/Documents/Solenoid Control/Solenoid Control-B_Cu.gbr'.
Plotted to '/Users/eldadzipori/Documents/Solenoid Control/Solenoid Control-F_Paste.gbr'.
Plotted to '/Users/eldadzipori/Documents/Solenoid Control/Solenoid Control-B_Paste.gbr'.
Plotted to '/Users/eldadzipori/Documents/Solenoid Control/Solenoid Control-F_Silkscreen.gbr'.
Plotted to '/Users/eldadzipori/Documents/Solenoid Control/Solenoid Control-B_Silkscreen.gbr'.
Plotted to '/Users/eldadzipori/Documents/Solenoid Control/Solenoid Control-F_Mask.gbr'.
Plotted to '/Users/eldadzipori/Documents/Solenoid Control/Solenoid Control-B_Mask.gbr'.
Plotted to '/Users/eldadzipori/Documents/Solenoid Control/Solenoid Control-Edge_Cuts.gbr'.
Created Gerber job file '/Users/eldadzipori/Documents/Solenoid Control/Solenoid Control-job.gbrjob'.
Info: Done.

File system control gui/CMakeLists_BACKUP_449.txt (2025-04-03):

cmake_minimum_required(VERSION 3.16)

# Project name and settings
project(BeerPongSentinel VERSION 0.1 LANGUAGES CXX)
add_definitions(-D_WIN32 -DWIN64)
set(CMAKE_AUTOUIC ON)
set(CMAKE_AUTOMOC ON)
set(CMAKE_AUTORCC ON)
set(CMAKE_CXX_STANDARD 17)
set(CMAKE_CXX_STANDARD_REQUIRED ON)

########################################################################
# Set these paths to match your system:
# Qt installation directory
set(CMAKE_PREFIX_PATH "C:/Qt/6.8.3/msvc2022_64")

# Spinnaker SDK path
set(SPINNAKER_SDK_PATH "C:/Program Files/Teledyne/Spinnaker")

# OpenCV build path -- now using the CUDA-enabled version
set(OPEN_CV_PATH "C:/opencv_cuda")

# Teknic SDK path (base directory)
set(TEKNIC_SDK_PATH "C:/Program Files (x86)/Teknic/ClearView/sdk")

set(EIGEN3_INCLUDE_DIR "C:/libs/eigen/eigen-3.4.0")
set(EIGEN3_UNSUPPORTED_DIR "C:/libs/eigen/eigen-3.4.0/unsupported")
########################################################################

set(QT_VERSION_MAJOR 6)
set(Qt6_DIR "${CMAKE_PREFIX_PATH}/lib/cmake/Qt6")

find_package(QT NAMES Qt6 REQUIRED COMPONENTS Widgets LinguistTools OpenGL OpenGLWidgets SerialPort Concurrent Qml)
find_package(Qt${QT_VERSION_MAJOR} REQUIRED COMPONENTS Widgets LinguistTools OpenGL OpenGLWidgets SerialPort Concurrent Qml)

set(TS_FILES BeerPongSentinel_en_CA.ts)

# List all your source files here
set(PROJECT_SOURCES
    main.cpp
    MainWindow.cpp
    MainWindow.h
    MainWindow.ui
    ${TS_FILES}
    config.json
    CameraCaptureThread.cpp
    CameraSetup.cpp
    CameraStreamWidget.cpp
    ImageProcessing.cpp
    AltitudeControl.cpp
    CameraCaptureThread.h
    CameraSetup.h
    CameraStreamWidget.h
    ImageProcessing.h
    AltitudeControl.h
    json.hpp
    CameraCalibration.cpp
    CameraCalibration.h
    AzimuthControl.cpp
    AzimuthControl.h
    YOLOInferenceWorker.h
)

if(${QT_VERSION_MAJOR} GREATER_EQUAL 6)
    qt_add_executable(BeerPongSentinel
        MANUAL_FINALIZATION
        ${PROJECT_SOURCES}
        config.json
        CameraCaptureThread.cpp CameraSetup.cpp CameraStreamWidget.cpp ImageProcessing.cpp
        CameraCaptureThread.h CameraSetup.h CameraStreamWidget.h ImageProcessing.h
        json.hpp
        CameraCalibration.cpp
        CameraCalibration.h
        ProcessTimer.h ProcessTimer.cpp
        YOLOInferenceWorker.h
        resources.qrc

    )
    qt_create_translation(QM_FILES ${CMAKE_SOURCE_DIR} ${TS_FILES})
else()
    if(ANDROID)
        add_library(BeerPongSentinel SHARED ${PROJECT_SOURCES})
    else()
        add_executable(BeerPongSentinel ${PROJECT_SOURCES})
    endif()
    qt5_create_translation(QM_FILES ${CMAKE_SOURCE_DIR} ${TS_FILES})
endif()

# Add include directories for external SDKs
include_directories("${SPINNAKER_SDK_PATH}/include")
include_directories("${OPEN_CV_PATH}/include")
include_directories("${TEKNIC_SDK_PATH}/inc")
include_directories("${EIGEN3_INCLUDE_DIR}")
include_directories("${EIGEN3_UNSUPPORTED_DIR}")

# Link directories for Spinnaker and OpenCV
link_directories("${SPINNAKER_SDK_PATH}/lib64/vs2015")
link_directories("${OPEN_CV_PATH}/x64/vc16/lib")

# get all the cuda opencv libraries
set(OpenCV_DIR "C:/opencv_cuda")
find_package(OpenCV REQUIRED)

# Link libraries:
target_link_libraries(BeerPongSentinel PRIVATE
    Qt${QT_VERSION_MAJOR}::Widgets
    "${SPINNAKER_SDK_PATH}/lib64/vs2015/Spinnaker_v140.lib"
    ${OpenCV_LIBS}
    "${TEKNIC_SDK_PATH}/sFoundation Source/sFoundation/win/Debug/x64/sFoundation20.lib"
    "${TEKNIC_SDK_PATH}/lib/win/Release/x64/sFoundation20.lib"
    Qt6::OpenGL
    opengl32
    Qt6::OpenGLWidgets
    Qt6::SerialPort
    Qt6::Concurrent
    Qt6::Qml
)

if(MSVC)
    if(CMAKE_SIZEOF_VOID_P EQUAL 8)
        set(PLATFORM_NAME "x64")
    else()
        set(PLATFORM_NAME "Win32")
    endif()
endif()

add_custom_command(TARGET BeerPongSentinel POST_BUILD
    COMMAND "C:/Program Files (x86)/Teknic/ClearView/sdk/examples/sFoundationCopy.bat" ${PLATFORM_NAME} $<CONFIG> "$<TARGET_FILE_DIR:BeerPongSentinel>"
    COMMENT "Copying sFoundation Files"
)

add_custom_command(TARGET BeerPongSentinel POST_BUILD
    COMMAND ${CMAKE_COMMAND} -E copy_directory "C:/Program Files/NVIDIA/CUDNN/v9.8/bin/12.8" "$<TARGET_FILE_DIR:BeerPongSentinel>"
    COMMENT "Copying all cuDNN DLLs to output directory"
)

if(${QT_VERSION} VERSION_LESS 6.1.0)
  set(BUNDLE_ID_OPTION MACOSX_BUNDLE_GUI_IDENTIFIER com.example.BeerPongSentinel)
endif()
set_target_properties(BeerPongSentinel PROPERTIES
    ${BUNDLE_ID_OPTION}
    MACOSX_BUNDLE_BUNDLE_VERSION ${PROJECT_VERSION}
    MACOSX_BUNDLE_SHORT_VERSION_STRING "${PROJECT_VERSION_MAJOR}.${PROJECT_VERSION_MINOR}"
    MACOSX_BUNDLE TRUE
    WIN32_EXECUTABLE TRUE
)

include(GNUInstallDirs)
install(TARGETS BeerPongSentinel
    BUNDLE DESTINATION .
    LIBRARY DESTINATION ${CMAKE_INSTALL_LIBDIR}
    RUNTIME DESTINATION ${CMAKE_INSTALL_BINDIR}
)

if(QT_VERSION_MAJOR EQUAL 6)
    qt_finalize_executable(BeerPongSentinel)
endif()

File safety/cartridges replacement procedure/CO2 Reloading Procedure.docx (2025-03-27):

# CO2 Reloading Procedures

Updated Oct 22, 2024

# Risks

## CO2 Cartridge Explosion

CO2 cartridge explodes during installation

Hazard | Most Significant (4)
Exposure | Medium (2)
Risk | Most Significant (8)

# Procedures

1. | Have two people for this procedure. One to perform the installation, one to watch over from a safe distance
2. | Both must wear a face shield
3. | Use an allan’s wrench to loosen up the screws under the CO2 cartridges
4. | Take out both CO2 cartridges
5. | Apply a drop of oil on the tip of the two new CO2 Cartridges
6. | Place the two new Cartridges in the magazine without tightening them
7. | Use the allan wrench to screw both cartridges until they are tight against the enclosure but no pressure is put on them
8. | Tightening the cartridge label as FIRST until you hear a small sound indicating the cartridge was pierced and then a little bit more.
9. | Tightening the other cartridge until you hear a small sound indicating the cartridge was pierced. Make sure there is no more leaking sound.

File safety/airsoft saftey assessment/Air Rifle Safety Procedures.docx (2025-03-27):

# Air Rifle Safety Plan & Procedures

Updated Oct 18, 2024

# Risks

## Indirect Fire

BB impact after ricochet.

Hazard | Significant (3)
Exposure | Significant (3)
Risk | Most Significant (9)

## Direct Fire

BB impact directly from the barrel of the rifle.

Hazard | Most Significant (4)
Exposure | Medium (2)
Risk | Significant (8)

## Compressed Gasses

CO2 gas cartridge at nearly 1000 psi

Hazard | Medium (2)
Exposure | Low (1)
Risk | Low (2)

## Sharp Objects

Potentially created by BB contact with fragile items

Hazard | Low (1)
Exposure | Low (1)
Risk | Low (1)

# Mitigations

## Engineering Controls

### Soft Capture Backstop

Decelerate the BB immediately after it passes through the target, do not provide surface for ricochet. The rifle must always point at the backstop when not safed.

Addresses: Indirect Fire

## Administrative Controls

### Rifle Safing

Safe the rife except immediately before, during, and after a test - put the rifle into a state where it is unable to fire in all situations except directly before, during, and after a test. This means removing the magazine. When the rifle is not safed, no one is allowed in front of the barrel.

Addresses: Indirect Fire, Direct Fire

### Rifle State Change Callouts

Verbal callout and callback when changing the safety state of the rifle - when the state of the rifle is changed to or from safe, it must be announced by the person making the change and verbally acknowledged by everyone present.

Addresses: Indirect Fire, Direct Fire

### High-Pressure Gas Acknowledgement

Inform participants of the presence of high-pressure gas

Addresses: Compressed gasses

Pinch hazard

### Separation of Equipment

The magazine, pellets, and rifle are not to be near each other when the equipment is unattended. This ensures that some random person cannot fire the rifle.

Addresses: All

## PPE

### Safety Glasses/Face Shields

All participants must wear safety glasses or a face shield at all times when the rifle is not safed.

Addresses: Indirect Fire

### Heavy Gloves

Note position of heavy gloves before testing - allows safe handling of any sharp objects that may be created

Addresses: Sharp Objects

# Procedures

These procedures are presented in checklist form to support the mitigations described above.

## Before Setup of Tests Involving Air Rifle

  All participants receive safety briefing on air rifle test
    All Risks are presented and described
    Zero Access to Firing Area control is explained and acknowledged
    Rifle Safing control is explained and acknowledged
    Rifle State Change Callouts control is explained and acknowledged
    High-Pressure Gas presence is acknowledgement
    Heavy Gloves location is described
    Safety briefing leader visually confirms that every participant is wearing safety glasses, and informs that they are not to be removed
  Soft capture backstop is installed and verified to be in good condition

The rifle may now be removed from storage and set up

Make it so that there's only one way for it to fire - 3d printed something

## Setup of Air Rifle

- Verbally announce and receive confirmation from each participant that it is now prohibited to pass forward of the barrel of the rifle.
- Set up the Air Rifle in the test location

May now proceed to testing, repeating the testing procedure as many times as required for the number of tests

## Test Involving Air Rifle

- Verify that the soft capture backstop in installed
- Verify that no one is forward of the barrel of the rifle
- Verbally announce and receive acknowledgement from everyone present that you are arming the rifle
- Arm the rifle
- Perform the test
- Disarm the rifle
- Verbally announce and receive acknowledgement from everyone present that the rifle is disarmed

Once tests are completed, the rifle can be stored

## Storing the Air Rifle

- Store the rifle in it's storage location
- Verbally announce and receive confirmation from each participant that the rifle has been stored and they can now move freely

## After Tests Involving Air Rifle

- Remove and inspect the Soft Capture Backstop
- If any safety incidents occurred, after the first test, or after major changes to the test procedure, conduct a safety debriefing and modify the safety plan and procedures as necessary.

Power off before removing magazine

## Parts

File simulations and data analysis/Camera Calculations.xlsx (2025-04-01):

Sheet: Sheet1
Camera Parameters |  |  |  |  | Environmental Parameters |  |  |  |  | Lens Parameters |  |  |  |  | Stereo Vision Parameters
Name | Value | Units | Source | Comments | Name | Value | Units | Source | Comments | Name | Value | Units | Source | Comments | Name | Value | Units | Source | Comments
Horizontal Resolution | 720 | px | https://www.flir.ca/products/blackfly-s-usb3/?vertical=machine+vision&segment=iis |  | Working Distance (WD) | 2 | m | https://www.edmundoptics.com/knowledge-center/application-notes/imaging/11-best-practices-for-better-imaging/ | 2-4 x HFOV | Focal Length (f) | 6 | mm | Temp lens |  | Calibration Projection Error | 0.60 | px | polina_test
Vertical Resolution | 540 | px | - |  | HFOV | 1.66 | m | https://www.edmundoptics.com/knowledge-center/application-notes/imaging/understanding-focal-length-and-field-of-view/ |  | Angular Field of View (AFOV) | 44.98 | deg | https://www.edmundoptics.com/knowledge-center/application-notes/imaging/understanding-focal-length-and-field-of-view/ |  | Absolute Uncertainty at WD | 1.38 | mm
Pixel Size | 6.9 | um | - |  | Ball Diameter (D) | 50 | mm | caliper measurement |  | Primary Magnification (m) | 0.00300 |  | https://www.edmundoptics.com/knowledge-center/application-notes/imaging/6-fundamental-parameters-of-an-imaging-system/ |  | Relative Uncertainty at WD (% of D) | 2.76%
Horizontal Sensor Length (H) | 4.97 | mm |  |  | Table Width | 1 | m |  |  | F-number (f/#, N) | 1.4 |  |  |  | Acceptable Relative Uncertainty at WD | 5%
Vertical Sensor Length (V) | 3.73 | mm |  |  | Table Length | 2.5 | m |  |  | Open Aperture Diameter (Ø) | 25.5 | mm | Temp lens |  | Angle of Each Camera to Baseline | 70 | deg
Sensor Format | 1/2.9 | " | - |  | HFOV | 2.69 |  |  |  | Actual Aperture Diameter (Ø) | 18.21 | mm |  |  | Dist from rotation center to barrel tip (R) | 300 | mm
IRC Filter Thickness | 1.00 | mm | https://www.flir.com/support-center/iis/machine-vision/application-note/selecting-a-lens-for-your-camera/ |  | WD | 3.25 | m |  |  | ξ_Object Space [lp/mm] | 0.217 | lp/mm | https://www.edmundoptics.com/knowledge-center/application-notes/imaging/resolution/ |  | Minimum discernable motor resolution (theta) | 0.44 | deg
Sensor Package Window Thickness | 0.50 | mm | - |  |  |  |  |  |  | ξ_Object Space [mm] | 2.30 | mm | - | Min resolved spot | Frames needed for prediction | 20
C-mount Back Flange Distance | 17.53 | mm | - |  |  |  |  |  |  | Circle of Confusion (CoC) | 0.006 | mm | https://www.capcam.org/theory/ | CoC should be slightly smaller than 1px (e.g. 90%) | Time for prediction | 250 | ms
Total Back Flange Distance (BFD) | 19.03 | mm |  |  |  |  |  |  |  | Hyperfocal Distance | 4146.8 | mm |  |  | Maximum exposure time | 12500 | us
ξ_Image Space | 72.46 | lp/mm | https://www.edmundoptics.com/knowledge-center/application-notes/imaging/resolution/ |  |  |  |  |  |  | Near Limit of Focus | 699.2 | mm
 |  |  |  |  |  |  |  |  |  | Far Limit of Focus | 1994.4 | mm
 |  |  |  |  |  |  |  |  |  | Depth of Field (DoF) | 2693.6 | mm | https://damienfournier.co/dof-the-simplified-formula-to-understand-dof/
 |  |  |  |  |  |  |  |  |  | Depth of Field (DoF) | 2.51 | m | - |  |  |  |  |  |  | 7.58389

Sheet: Sheet2
Camera Resolution Width (px) | 720 | Maximum Shutter Speed (s) | 0.0019157
Horizontal FOV (m)\Maximum Ball Speed (m/s) | 0.5 | 1 | 1.5 | 2 | 2.5 | 3 | 3.5 | 4 | 4.5 | 5 | 5.5 | 6 | 6.5 | 7 | 7.5 | 8 | 8.5 | 9 | 9.5 | 10
0.1 | 0.0002778 | 0.0001389 | 0.0000926 | 0.0000694 | 0.0000556 | 0.0000463 | 0.0000397 | 0.0000347 | 0.0000309 | 0.0000278 | 0.0000253 | 0.0000231 | 0.0000214 | 0.0000198 | 0.0000185 | 0.0000174 | 0.0000163 | 0.0000154 | 0.0000146 | 0.0000139
0.2 | 0.0005556 | 0.0002778 | 0.0001852 | 0.0001389 | 0.0001111 | 0.0000926 | 0.0000794 | 0.0000694 | 0.0000617 | 0.0000556 | 0.0000505 | 0.0000463 | 0.0000427 | 0.0000397 | 0.0000370 | 0.0000347 | 0.0000327 | 0.0000309 | 0.0000292 | 0.0000278
0.3 | 0.0008333 | 0.0004167 | 0.0002778 | 0.0002083 | 0.0001667 | 0.0001389 | 0.0001190 | 0.0001042 | 0.0000926 | 0.0000833 | 0.0000758 | 0.0000694 | 0.0000641 | 0.0000595 | 0.0000556 | 0.0000521 | 0.0000490 | 0.0000463 | 0.0000439 | 0.0000417
0.4 | 0.0011111 | 0.0005556 | 0.0003704 | 0.0002778 | 0.0002222 | 0.0001852 | 0.0001587 | 0.0001389 | 0.0001235 | 0.0001111 | 0.0001010 | 0.0000926 | 0.0000855 | 0.0000794 | 0.0000741 | 0.0000694 | 0.0000654 | 0.0000617 | 0.0000585 | 0.0000556
0.5 | 0.0013889 | 0.0006944 | 0.0004630 | 0.0003472 | 0.0002778 | 0.0002315 | 0.0001984 | 0.0001736 | 0.0001543 | 0.0001389 | 0.0001263 | 0.0001157 | 0.0001068 | 0.0000992 | 0.0000926 | 0.0000868 | 0.0000817 | 0.0000772 | 0.0000731 | 0.0000694
0.6 | 0.0016667 | 0.0008333 | 0.0005556 | 0.0004167 | 0.0003333 | 0.0002778 | 0.0002381 | 0.0002083 | 0.0001852 | 0.0001667 | 0.0001515 | 0.0001389 | 0.0001282 | 0.0001190 | 0.0001111 | 0.0001042 | 0.0000980 | 0.0000926 | 0.0000877 | 0.0000833
0.7 | 0.0019444 | 0.0009722 | 0.0006481 | 0.0004861 | 0.0003889 | 0.0003241 | 0.0002778 | 0.0002431 | 0.0002160 | 0.0001944 | 0.0001768 | 0.0001620 | 0.0001496 | 0.0001389 | 0.0001296 | 0.0001215 | 0.0001144 | 0.0001080 | 0.0001023 | 0.0000972
0.8 | 0.0022222 | 0.0011111 | 0.0007407 | 0.0005556 | 0.0004444 | 0.0003704 | 0.0003175 | 0.0002778 | 0.0002469 | 0.0002222 | 0.0002020 | 0.0001852 | 0.0001709 | 0.0001587 | 0.0001481 | 0.0001389 | 0.0001307 | 0.0001235 | 0.0001170 | 0.0001111
0.9 | 0.0025000 | 0.0012500 | 0.0008333 | 0.0006250 | 0.0005000 | 0.0004167 | 0.0003571 | 0.0003125 | 0.0002778 | 0.0002500 | 0.0002273 | 0.0002083 | 0.0001923 | 0.0001786 | 0.0001667 | 0.0001563 | 0.0001471 | 0.0001389 | 0.0001316 | 0.0001250
1 | 0.0027778 | 0.0013889 | 0.0009259 | 0.0006944 | 0.0005556 | 0.0004630 | 0.0003968 | 0.0003472 | 0.0003086 | 0.0002778 | 0.0002525 | 0.0002315 | 0.0002137 | 0.0001984 | 0.0001852 | 0.0001736 | 0.0001634 | 0.0001543 | 0.0001462 | 0.0001389
1.1 | 0.0030556 | 0.0015278 | 0.0010185 | 0.0007639 | 0.0006111 | 0.0005093 | 0.0004365 | 0.0003819 | 0.0003395 | 0.0003056 | 0.0002778 | 0.0002546 | 0.0002350 | 0.0002183 | 0.0002037 | 0.0001910 | 0.0001797 | 0.0001698 | 0.0001608 | 0.0001528
1.2 | 0.0033333 | 0.0016667 | 0.0011111 | 0.0008333 | 0.0006667 | 0.0005556 | 0.0004762 | 0.0004167 | 0.0003704 | 0.0003333 | 0.0003030 | 0.0002778 | 0.0002564 | 0.0002381 | 0.0002222 | 0.0002083 | 0.0001961 | 0.0001852 | 0.0001754 | 0.0001667
1.3 | 0.0036111 | 0.0018056 | 0.0012037 | 0.0009028 | 0.0007222 | 0.0006019 | 0.0005159 | 0.0004514 | 0.0004012 | 0.0003611 | 0.0003283 | 0.0003009 | 0.0002778 | 0.0002579 | 0.0002407 | 0.0002257 | 0.0002124 | 0.0002006 | 0.0001901 | 0.0001806
1.4 | 0.0038889 | 0.0019444 | 0.0012963 | 0.0009722 | 0.0007778 | 0.0006481 | 0.0005556 | 0.0004861 | 0.0004321 | 0.0003889 | 0.0003535 | 0.0003241 | 0.0002991 | 0.0002778 | 0.0002593 | 0.0002431 | 0.0002288 | 0.0002160 | 0.0002047 | 0.0001944
1.5 | 0.0041667 | 0.0020833 | 0.0013889 | 0.0010417 | 0.0008333 | 0.0006944 | 0.0005952 | 0.0005208 | 0.0004630 | 0.0004167 | 0.0003788 | 0.0003472 | 0.0003205 | 0.0002976 | 0.0002778 | 0.0002604 | 0.0002451 | 0.0002315 | 0.0002193 | 0.0002083
1.6 | 0.0044444 | 0.0022222 | 0.0014815 | 0.0011111 | 0.0008889 | 0.0007407 | 0.0006349 | 0.0005556 | 0.0004938 | 0.0004444 | 0.0004040 | 0.0003704 | 0.0003419 | 0.0003175 | 0.0002963 | 0.0002778 | 0.0002614 | 0.0002469 | 0.0002339 | 0.0002222
1.7 | 0.0047222 | 0.0023611 | 0.0015741 | 0.0011806 | 0.0009444 | 0.0007870 | 0.0006746 | 0.0005903 | 0.0005247 | 0.0004722 | 0.0004293 | 0.0003935 | 0.0003632 | 0.0003373 | 0.0003148 | 0.0002951 | 0.0002778 | 0.0002623 | 0.0002485 | 0.0002361
1.8 | 0.0050000 | 0.0025000 | 0.0016667 | 0.0012500 | 0.0010000 | 0.0008333 | 0.0007143 | 0.0006250 | 0.0005556 | 0.0005000 | 0.0004545 | 0.0004167 | 0.0003846 | 0.0003571 | 0.0003333 | 0.0003125 | 0.0002941 | 0.0002778 | 0.0002632 | 0.0002500
1.9 | 0.0052778 | 0.0026389 | 0.0017593 | 0.0013194 | 0.0010556 | 0.0008796 | 0.0007540 | 0.0006597 | 0.0005864 | 0.0005278 | 0.0004798 | 0.0004398 | 0.0004060 | 0.0003770 | 0.0003519 | 0.0003299 | 0.0003105 | 0.0002932 | 0.0002778 | 0.0002639
2 | 0.0055556 | 0.0027778 | 0.0018519 | 0.0013889 | 0.0011111 | 0.0009259 | 0.0007937 | 0.0006944 | 0.0006173 | 0.0005556 | 0.0005051 | 0.0004630 | 0.0004274 | 0.0003968 | 0.0003704 | 0.0003472 | 0.0003268 | 0.0003086 | 0.0002924 | 0.0002778
2.1 | 0.0058333 | 0.0029167 | 0.0019444 | 0.0014583 | 0.0011667 | 0.0009722 | 0.0008333 | 0.0007292 | 0.0006481 | 0.0005833 | 0.0005303 | 0.0004861 | 0.0004487 | 0.0004167 | 0.0003889 | 0.0003646 | 0.0003431 | 0.0003241 | 0.0003070 | 0.0002917
2.2 | 0.0061111 | 0.0030556 | 0.0020370 | 0.0015278 | 0.0012222 | 0.0010185 | 0.0008730 | 0.0007639 | 0.0006790 | 0.0006111 | 0.0005556 | 0.0005093 | 0.0004701 | 0.0004365 | 0.0004074 | 0.0003819 | 0.0003595 | 0.0003395 | 0.0003216 | 0.0003056
2.3 | 0.0063889 | 0.0031944 | 0.0021296 | 0.0015972 | 0.0012778 | 0.0010648 | 0.0009127 | 0.0007986 | 0.0007099 | 0.0006389 | 0.0005808 | 0.0005324 | 0.0004915 | 0.0004563 | 0.0004259 | 0.0003993 | 0.0003758 | 0.0003549 | 0.0003363 | 0.0003194
2.4 | 0.0066667 | 0.0033333 | 0.0022222 | 0.0016667 | 0.0013333 | 0.0011111 | 0.0009524 | 0.0008333 | 0.0007407 | 0.0006667 | 0.0006061 | 0.0005556 | 0.0005128 | 0.0004762 | 0.0004444 | 0.0004167 | 0.0003922 | 0.0003704 | 0.0003509 | 0.0003333
2.5 | 0.0069444 | 0.0034722 | 0.0023148 | 0.0017361 | 0.0013889 | 0.0011574 | 0.0009921 | 0.0008681 | 0.0007716 | 0.0006944 | 0.0006313 | 0.0005787 | 0.0005342 | 0.0004960 | 0.0004630 | 0.0004340 | 0.0004085 | 0.0003858 | 0.0003655 | 0.0003472
2.6 | 0.0072222 | 0.0036111 | 0.0024074 | 0.0018056 | 0.0014444 | 0.0012037 | 0.0010317 | 0.0009028 | 0.0008025 | 0.0007222 | 0.0006566 | 0.0006019 | 0.0005556 | 0.0005159 | 0.0004815 | 0.0004514 | 0.0004248 | 0.0004012 | 0.0003801 | 0.0003611
2.7 | 0.0075000 | 0.0037500 | 0.0025000 | 0.0018750 | 0.0015000 | 0.0012500 | 0.0010714 | 0.0009375 | 0.0008333 | 0.0007500 | 0.0006818 | 0.0006250 | 0.0005769 | 0.0005357 | 0.0005000 | 0.0004687 | 0.0004412 | 0.0004167 | 0.0003947 | 0.0003750
2.8 | 0.0077778 | 0.0038889 | 0.0025926 | 0.0019444 | 0.0015556 | 0.0012963 | 0.0011111 | 0.0009722 | 0.0008642 | 0.0007778 | 0.0007071 | 0.0006481 | 0.0005983 | 0.0005556 | 0.0005185 | 0.0004861 | 0.0004575 | 0.0004321 | 0.0004094 | 0.0003889
2.9 | 0.0080556 | 0.0040278 | 0.0026852 | 0.0020139 | 0.0016111 | 0.0013426 | 0.0011508 | 0.0010069 | 0.0008951 | 0.0008056 | 0.0007323 | 0.0006713 | 0.0006197 | 0.0005754 | 0.0005370 | 0.0005035 | 0.0004739 | 0.0004475 | 0.0004240 | 0.0004028
3 | 0.0083333 | 0.0041667 | 0.0027778 | 0.0020833 | 0.0016667 | 0.0013889 | 0.0011905 | 0.0010417 | 0.0009259 | 0.0008333 | 0.0007576 | 0.0006944 | 0.0006410 | 0.0005952 | 0.0005556 | 0.0005208 | 0.0004902 | 0.0004630 | 0.0004386 | 0.0004167
3.1 | 0.0086111 | 0.0043056 | 0.0028704 | 0.0021528 | 0.0017222 | 0.0014352 | 0.0012302 | 0.0010764 | 0.0009568 | 0.0008611 | 0.0007828 | 0.0007176 | 0.0006624 | 0.0006151 | 0.0005741 | 0.0005382 | 0.0005065 | 0.0004784 | 0.0004532 | 0.0004306
3.2 | 0.0088889 | 0.0044444 | 0.0029630 | 0.0022222 | 0.0017778 | 0.0014815 | 0.0012698 | 0.0011111 | 0.0009877 | 0.0008889 | 0.0008081 | 0.0007407 | 0.0006838 | 0.0006349 | 0.0005926 | 0.0005556 | 0.0005229 | 0.0004938 | 0.0004678 | 0.0004444
3.3 | 0.0091667 | 0.0045833 | 0.0030556 | 0.0022917 | 0.0018333 | 0.0015278 | 0.0013095 | 0.0011458 | 0.0010185 | 0.0009167 | 0.0008333 | 0.0007639 | 0.0007051 | 0.0006548 | 0.0006111 | 0.0005729 | 0.0005392 | 0.0005093 | 0.0004825 | 0.0004583
3.4 | 0.0094444 | 0.0047222 | 0.0031481 | 0.0023611 | 0.0018889 | 0.0015741 | 0.0013492 | 0.0011806 | 0.0010494 | 0.0009444 | 0.0008586 | 0.0007870 | 0.0007265 | 0.0006746 | 0.0006296 | 0.0005903 | 0.0005556 | 0.0005247 | 0.0004971 | 0.0004722
3.5 | 0.0097222 | 0.0048611 | 0.0032407 | 0.0024306 | 0.0019444 | 0.0016204 | 0.0013889 | 0.0012153 | 0.0010802 | 0.0009722 | 0.0008838 | 0.0008102 | 0.0007479 | 0.0006944 | 0.0006481 | 0.0006076 | 0.0005719 | 0.0005401 | 0.0005117 | 0.0004861
3.6 | 0.0100000 | 0.0050000 | 0.0033333 | 0.0025000 | 0.0020000 | 0.0016667 | 0.0014286 | 0.0012500 | 0.0011111 | 0.0010000 | 0.0009091 | 0.0008333 | 0.0007692 | 0.0007143 | 0.0006667 | 0.0006250 | 0.0005882 | 0.0005556 | 0.0005263 | 0.0005000
3.7 | 0.0102778 | 0.0051389 | 0.0034259 | 0.0025694 | 0.0020556 | 0.0017130 | 0.0014683 | 0.0012847 | 0.0011420 | 0.0010278 | 0.0009343 | 0.0008565 | 0.0007906 | 0.0007341 | 0.0006852 | 0.0006424 | 0.0006046 | 0.0005710 | 0.0005409 | 0.0005139
3.8 | 0.0105556 | 0.0052778 | 0.0035185 | 0.0026389 | 0.0021111 | 0.0017593 | 0.0015079 | 0.0013194 | 0.0011728 | 0.0010556 | 0.0009596 | 0.0008796 | 0.0008120 | 0.0007540 | 0.0007037 | 0.0006597 | 0.0006209 | 0.0005864 | 0.0005556 | 0.0005278
3.9 | 0.0108333 | 0.0054167 | 0.0036111 | 0.0027083 | 0.0021667 | 0.0018056 | 0.0015476 | 0.0013542 | 0.0012037 | 0.0010833 | 0.0009848 | 0.0009028 | 0.0008333 | 0.0007738 | 0.0007222 | 0.0006771 | 0.0006373 | 0.0006019 | 0.0005702 | 0.0005417
4 | 0.0111111 | 0.0055556 | 0.0037037 | 0.0027778 | 0.0022222 | 0.0018519 | 0.0015873 | 0.0013889 | 0.0012346 | 0.0011111 | 0.0010101 | 0.0009259 | 0.0008547 | 0.0007937 | 0.0007407 | 0.0006944 | 0.0006536 | 0.0006173 | 0.0005848 | 0.0005556
4.1 | 0.0113889 | 0.0056944 | 0.0037963 | 0.0028472 | 0.0022778 | 0.0018981 | 0.0016270 | 0.0014236 | 0.0012654 | 0.0011389 | 0.0010354 | 0.0009491 | 0.0008761 | 0.0008135 | 0.0007593 | 0.0007118 | 0.0006699 | 0.0006327 | 0.0005994 | 0.0005694
4.2 | 0.0116667 | 0.0058333 | 0.0038889 | 0.0029167 | 0.0023333 | 0.0019444 | 0.0016667 | 0.0014583 | 0.0012963 | 0.0011667 | 0.0010606 | 0.0009722 | 0.0008974 | 0.0008333 | 0.0007778 | 0.0007292 | 0.0006863 | 0.0006481 | 0.0006140 | 0.0005833
4.3 | 0.0119444 | 0.0059722 | 0.0039815 | 0.0029861 | 0.0023889 | 0.0019907 | 0.0017063 | 0.0014931 | 0.0013272 | 0.0011944 | 0.0010859 | 0.0009954 | 0.0009188 | 0.0008532 | 0.0007963 | 0.0007465 | 0.0007026 | 0.0006636 | 0.0006287 | 0.0005972
4.4 | 0.0122222 | 0.0061111 | 0.0040741 | 0.0030556 | 0.0024444 | 0.0020370 | 0.0017460 | 0.0015278 | 0.0013580 | 0.0012222 | 0.0011111 | 0.0010185 | 0.0009402 | 0.0008730 | 0.0008148 | 0.0007639 | 0.0007190 | 0.0006790 | 0.0006433 | 0.0006111
4.5 | 0.0125000 | 0.0062500 | 0.0041667 | 0.0031250 | 0.0025000 | 0.0020833 | 0.0017857 | 0.0015625 | 0.0013889 | 0.0012500 | 0.0011364 | 0.0010417 | 0.0009615 | 0.0008929 | 0.0008333 | 0.0007813 | 0.0007353 | 0.0006944 | 0.0006579 | 0.0006250
4.6 | 0.0127778 | 0.0063889 | 0.0042593 | 0.0031944 | 0.0025556 | 0.0021296 | 0.0018254 | 0.0015972 | 0.0014198 | 0.0012778 | 0.0011616 | 0.0010648 | 0.0009829 | 0.0009127 | 0.0008519 | 0.0007986 | 0.0007516 | 0.0007099 | 0.0006725 | 0.0006389
4.7 | 0.0130556 | 0.0065278 | 0.0043519 | 0.0032639 | 0.0026111 | 0.0021759 | 0.0018651 | 0.0016319 | 0.0014506 | 0.0013056 | 0.0011869 | 0.0010880 | 0.0010043 | 0.0009325 | 0.0008704 | 0.0008160 | 0.0007680 | 0.0007253 | 0.0006871 | 0.0006528
4.8 | 0.0133333 | 0.0066667 | 0.0044444 | 0.0033333 | 0.0026667 | 0.0022222 | 0.0019048 | 0.0016667 | 0.0014815 | 0.0013333 | 0.0012121 | 0.0011111 | 0.0010256 | 0.0009524 | 0.0008889 | 0.0008333 | 0.0007843 | 0.0007407 | 0.0007018 | 0.0006667
4.9 | 0.0136111 | 0.0068056 | 0.0045370 | 0.0034028 | 0.0027222 | 0.0022685 | 0.0019444 | 0.0017014 | 0.0015123 | 0.0013611 | 0.0012374 | 0.0011343 | 0.0010470 | 0.0009722 | 0.0009074 | 0.0008507 | 0.0008007 | 0.0007562 | 0.0007164 | 0.0006806
5 | 0.0138889 | 0.0069444 | 0.0046296 | 0.0034722 | 0.0027778 | 0.0023148 | 0.0019841 | 0.0017361 | 0.0015432 | 0.0013889 | 0.0012626 | 0.0011574 | 0.0010684 | 0.0009921 | 0.0009259 | 0.0008681 | 0.0008170 | 0.0007716 | 0.0007310 | 0.0006944
5.1 | 0.0141667 | 0.0070833 | 0.0047222 | 0.0035417 | 0.0028333 | 0.0023611 | 0.0020238 | 0.0017708 | 0.0015741 | 0.0014167 | 0.0012879 | 0.0011806 | 0.0010897 | 0.0010119 | 0.0009444 | 0.0008854 | 0.0008333 | 0.0007870 | 0.0007456 | 0.0007083
5.2 | 0.0144444 | 0.0072222 | 0.0048148 | 0.0036111 | 0.0028889 | 0.0024074 | 0.0020635 | 0.0018056 | 0.0016049 | 0.0014444 | 0.0013131 | 0.0012037 | 0.0011111 | 0.0010317 | 0.0009630 | 0.0009028 | 0.0008497 | 0.0008025 | 0.0007602 | 0.0007222
5.3 | 0.0147222 | 0.0073611 | 0.0049074 | 0.0036806 | 0.0029444 | 0.0024537 | 0.0021032 | 0.0018403 | 0.0016358 | 0.0014722 | 0.0013384 | 0.0012269 | 0.0011325 | 0.0010516 | 0.0009815 | 0.0009201 | 0.0008660 | 0.0008179 | 0.0007749 | 0.0007361
5.4 | 0.0150000 | 0.0075000 | 0.0050000 | 0.0037500 | 0.0030000 | 0.0025000 | 0.0021429 | 0.0018750 | 0.0016667 | 0.0015000 | 0.0013636 | 0.0012500 | 0.0011538 | 0.0010714 | 0.0010000 | 0.0009375 | 0.0008824 | 0.0008333 | 0.0007895 | 0.0007500
5.5 | 0.0152778 | 0.0076389 | 0.0050926 | 0.0038194 | 0.0030556 | 0.0025463 | 0.0021825 | 0.0019097 | 0.0016975 | 0.0015278 | 0.0013889 | 0.0012731 | 0.0011752 | 0.0010913 | 0.0010185 | 0.0009549 | 0.0008987 | 0.0008488 | 0.0008041 | 0.0007639
5.6 | 0.0155556 | 0.0077778 | 0.0051852 | 0.0038889 | 0.0031111 | 0.0025926 | 0.0022222 | 0.0019444 | 0.0017284 | 0.0015556 | 0.0014141 | 0.0012963 | 0.0011966 | 0.0011111 | 0.0010370 | 0.0009722 | 0.0009150 | 0.0008642 | 0.0008187 | 0.0007778
5.7 | 0.0158333 | 0.0079167 | 0.0052778 | 0.0039583 | 0.0031667 | 0.0026389 | 0.0022619 | 0.0019792 | 0.0017593 | 0.0015833 | 0.0014394 | 0.0013194 | 0.0012179 | 0.0011310 | 0.0010556 | 0.0009896 | 0.0009314 | 0.0008796 | 0.0008333 | 0.0007917
5.8 | 0.0161111 | 0.0080556 | 0.0053704 | 0.0040278 | 0.0032222 | 0.0026852 | 0.0023016 | 0.0020139 | 0.0017901 | 0.0016111 | 0.0014646 | 0.0013426 | 0.0012393 | 0.0011508 | 0.0010741 | 0.0010069 | 0.0009477 | 0.0008951 | 0.0008480 | 0.0008056
5.9 | 0.0163889 | 0.0081944 | 0.0054630 | 0.0040972 | 0.0032778 | 0.0027315 | 0.0023413 | 0.0020486 | 0.0018210 | 0.0016389 | 0.0014899 | 0.0013657 | 0.0012607 | 0.0011706 | 0.0010926 | 0.0010243 | 0.0009641 | 0.0009105 | 0.0008626 | 0.0008194
6 | 0.0166667 | 0.0083333 | 0.0055556 | 0.0041667 | 0.0033333 | 0.0027778 | 0.0023810 | 0.0020833 | 0.0018519 | 0.0016667 | 0.0015152 | 0.0013889 | 0.0012821 | 0.0011905 | 0.0011111 | 0.0010417 | 0.0009804 | 0.0009259 | 0.0008772 | 0.0008333
6.1 | 0.0169444 | 0.0084722 | 0.0056481 | 0.0042361 | 0.0033889 | 0.0028241 | 0.0024206 | 0.0021181 | 0.0018827 | 0.0016944 | 0.0015404 | 0.0014120 | 0.0013034 | 0.0012103 | 0.0011296 | 0.0010590 | 0.0009967 | 0.0009414 | 0.0008918 | 0.0008472
6.2 | 0.0172222 | 0.0086111 | 0.0057407 | 0.0043056 | 0.0034444 | 0.0028704 | 0.0024603 | 0.0021528 | 0.0019136 | 0.0017222 | 0.0015657 | 0.0014352 | 0.0013248 | 0.0012302 | 0.0011481 | 0.0010764 | 0.0010131 | 0.0009568 | 0.0009064 | 0.0008611
6.3 | 0.0175000 | 0.0087500 | 0.0058333 | 0.0043750 | 0.0035000 | 0.0029167 | 0.0025000 | 0.0021875 | 0.0019444 | 0.0017500 | 0.0015909 | 0.0014583 | 0.0013462 | 0.0012500 | 0.0011667 | 0.0010938 | 0.0010294 | 0.0009722 | 0.0009211 | 0.0008750
6.4 | 0.0177778 | 0.0088889 | 0.0059259 | 0.0044444 | 0.0035556 | 0.0029630 | 0.0025397 | 0.0022222 | 0.0019753 | 0.0017778 | 0.0016162 | 0.0014815 | 0.0013675 | 0.0012698 | 0.0011852 | 0.0011111 | 0.0010458 | 0.0009877 | 0.0009357 | 0.0008889
6.5 | 0.0180556 | 0.0090278 | 0.0060185 | 0.0045139 | 0.0036111 | 0.0030093 | 0.0025794 | 0.0022569 | 0.0020062 | 0.0018056 | 0.0016414 | 0.0015046 | 0.0013889 | 0.0012897 | 0.0012037 | 0.0011285 | 0.0010621 | 0.0010031 | 0.0009503 | 0.0009028
6.6 | 0.0183333 | 0.0091667 | 0.0061111 | 0.0045833 | 0.0036667 | 0.0030556 | 0.0026190 | 0.0022917 | 0.0020370 | 0.0018333 | 0.0016667 | 0.0015278 | 0.0014103 | 0.0013095 | 0.0012222 | 0.0011458 | 0.0010784 | 0.0010185 | 0.0009649 | 0.0009167
6.7 | 0.0186111 | 0.0093056 | 0.0062037 | 0.0046528 | 0.0037222 | 0.0031019 | 0.0026587 | 0.0023264 | 0.0020679 | 0.0018611 | 0.0016919 | 0.0015509 | 0.0014316 | 0.0013294 | 0.0012407 | 0.0011632 | 0.0010948 | 0.0010340 | 0.0009795 | 0.0009306
6.8 | 0.0188889 | 0.0094444 | 0.0062963 | 0.0047222 | 0.0037778 | 0.0031481 | 0.0026984 | 0.0023611 | 0.0020988 | 0.0018889 | 0.0017172 | 0.0015741 | 0.0014530 | 0.0013492 | 0.0012593 | 0.0011806 | 0.0011111 | 0.0010494 | 0.0009942 | 0.0009444
6.9 | 0.0191667 | 0.0095833 | 0.0063889 | 0.0047917 | 0.0038333 | 0.0031944 | 0.0027381 | 0.0023958 | 0.0021296 | 0.0019167 | 0.0017424 | 0.0015972 | 0.0014744 | 0.0013690 | 0.0012778 | 0.0011979 | 0.0011275 | 0.0010648 | 0.0010088 | 0.0009583
7 | 0.0194444 | 0.0097222 | 0.0064815 | 0.0048611 | 0.0038889 | 0.0032407 | 0.0027778 | 0.0024306 | 0.0021605 | 0.0019444 | 0.0017677 | 0.0016204 | 0.0014957 | 0.0013889 | 0.0012963 | 0.0012153 | 0.0011438 | 0.0010802 | 0.0010234 | 0.0009722
7.1 | 0.0197222 | 0.0098611 | 0.0065741 | 0.0049306 | 0.0039444 | 0.0032870 | 0.0028175 | 0.0024653 | 0.0021914 | 0.0019722 | 0.0017929 | 0.0016435 | 0.0015171 | 0.0014087 | 0.0013148 | 0.0012326 | 0.0011601 | 0.0010957 | 0.0010380 | 0.0009861
7.2 | 0.0200000 | 0.0100000 | 0.0066667 | 0.0050000 | 0.0040000 | 0.0033333 | 0.0028571 | 0.0025000 | 0.0022222 | 0.0020000 | 0.0018182 | 0.0016667 | 0.0015385 | 0.0014286 | 0.0013333 | 0.0012500 | 0.0011765 | 0.0011111 | 0.0010526 | 0.0010000
7.3 | 0.0202778 | 0.0101389 | 0.0067593 | 0.0050694 | 0.0040556 | 0.0033796 | 0.0028968 | 0.0025347 | 0.0022531 | 0.0020278 | 0.0018434 | 0.0016898 | 0.0015598 | 0.0014484 | 0.0013519 | 0.0012674 | 0.0011928 | 0.0011265 | 0.0010673 | 0.0010139
7.4 | 0.0205556 | 0.0102778 | 0.0068519 | 0.0051389 | 0.0041111 | 0.0034259 | 0.0029365 | 0.0025694 | 0.0022840 | 0.0020556 | 0.0018687 | 0.0017130 | 0.0015812 | 0.0014683 | 0.0013704 | 0.0012847 | 0.0012092 | 0.0011420 | 0.0010819 | 0.0010278
7.5 | 0.0208333 | 0.0104167 | 0.0069444 | 0.0052083 | 0.0041667 | 0.0034722 | 0.0029762 | 0.0026042 | 0.0023148 | 0.0020833 | 0.0018939 | 0.0017361 | 0.0016026 | 0.0014881 | 0.0013889 | 0.0013021 | 0.0012255 | 0.0011574 | 0.0010965 | 0.0010417
7.6 | 0.0211111 | 0.0105556 | 0.0070370 | 0.0052778 | 0.0042222 | 0.0035185 | 0.0030159 | 0.0026389 | 0.0023457 | 0.0021111 | 0.0019192 | 0.0017593 | 0.0016239 | 0.0015079 | 0.0014074 | 0.0013194 | 0.0012418 | 0.0011728 | 0.0011111 | 0.0010556
7.7 | 0.0213889 | 0.0106944 | 0.0071296 | 0.0053472 | 0.0042778 | 0.0035648 | 0.0030556 | 0.0026736 | 0.0023765 | 0.0021389 | 0.0019444 | 0.0017824 | 0.0016453 | 0.0015278 | 0.0014259 | 0.0013368 | 0.0012582 | 0.0011883 | 0.0011257 | 0.0010694
7.8 | 0.0216667 | 0.0108333 | 0.0072222 | 0.0054167 | 0.0043333 | 0.0036111 | 0.0030952 | 0.0027083 | 0.0024074 | 0.0021667 | 0.0019697 | 0.0018056 | 0.0016667 | 0.0015476 | 0.0014444 | 0.0013542 | 0.0012745 | 0.0012037 | 0.0011404 | 0.0010833
7.9 | 0.0219444 | 0.0109722 | 0.0073148 | 0.0054861 | 0.0043889 | 0.0036574 | 0.0031349 | 0.0027431 | 0.0024383 | 0.0021944 | 0.0019949 | 0.0018287 | 0.0016880 | 0.0015675 | 0.0014630 | 0.0013715 | 0.0012908 | 0.0012191 | 0.0011550 | 0.0010972
8 | 0.0222222 | 0.0111111 | 0.0074074 | 0.0055556 | 0.0044444 | 0.0037037 | 0.0031746 | 0.0027778 | 0.0024691 | 0.0022222 | 0.0020202 | 0.0018519 | 0.0017094 | 0.0015873 | 0.0014815 | 0.0013889 | 0.0013072 | 0.0012346 | 0.0011696 | 0.0011111
8.1 | 0.0225000 | 0.0112500 | 0.0075000 | 0.0056250 | 0.0045000 | 0.0037500 | 0.0032143 | 0.0028125 | 0.0025000 | 0.0022500 | 0.0020455 | 0.0018750 | 0.0017308 | 0.0016071 | 0.0015000 | 0.0014062 | 0.0013235 | 0.0012500 | 0.0011842 | 0.0011250
8.2 | 0.0227778 | 0.0113889 | 0.0075926 | 0.0056944 | 0.0045556 | 0.0037963 | 0.0032540 | 0.0028472 | 0.0025309 | 0.0022778 | 0.0020707 | 0.0018981 | 0.0017521 | 0.0016270 | 0.0015185 | 0.0014236 | 0.0013399 | 0.0012654 | 0.0011988 | 0.0011389
8.3 | 0.0230556 | 0.0115278 | 0.0076852 | 0.0057639 | 0.0046111 | 0.0038426 | 0.0032937 | 0.0028819 | 0.0025617 | 0.0023056 | 0.0020960 | 0.0019213 | 0.0017735 | 0.0016468 | 0.0015370 | 0.0014410 | 0.0013562 | 0.0012809 | 0.0012135 | 0.0011528
8.4 | 0.0233333 | 0.0116667 | 0.0077778 | 0.0058333 | 0.0046667 | 0.0038889 | 0.0033333 | 0.0029167 | 0.0025926 | 0.0023333 | 0.0021212 | 0.0019444 | 0.0017949 | 0.0016667 | 0.0015556 | 0.0014583 | 0.0013725 | 0.0012963 | 0.0012281 | 0.0011667
8.5 | 0.0236111 | 0.0118056 | 0.0078704 | 0.0059028 | 0.0047222 | 0.0039352 | 0.0033730 | 0.0029514 | 0.0026235 | 0.0023611 | 0.0021465 | 0.0019676 | 0.0018162 | 0.0016865 | 0.0015741 | 0.0014757 | 0.0013889 | 0.0013117 | 0.0012427 | 0.0011806
8.6 | 0.0238889 | 0.0119444 | 0.0079630 | 0.0059722 | 0.0047778 | 0.0039815 | 0.0034127 | 0.0029861 | 0.0026543 | 0.0023889 | 0.0021717 | 0.0019907 | 0.0018376 | 0.0017063 | 0.0015926 | 0.0014931 | 0.0014052 | 0.0013272 | 0.0012573 | 0.0011944
8.7 | 0.0241667 | 0.0120833 | 0.0080556 | 0.0060417 | 0.0048333 | 0.0040278 | 0.0034524 | 0.0030208 | 0.0026852 | 0.0024167 | 0.0021970 | 0.0020139 | 0.0018590 | 0.0017262 | 0.0016111 | 0.0015104 | 0.0014216 | 0.0013426 | 0.0012719 | 0.0012083
8.8 | 0.0244444 | 0.0122222 | 0.0081481 | 0.0061111 | 0.0048889 | 0.0040741 | 0.0034921 | 0.0030556 | 0.0027160 | 0.0024444 | 0.0022222 | 0.0020370 | 0.0018803 | 0.0017460 | 0.0016296 | 0.0015278 | 0.0014379 | 0.0013580 | 0.0012865 | 0.0012222
8.9 | 0.0247222 | 0.0123611 | 0.0082407 | 0.0061806 | 0.0049444 | 0.0041204 | 0.0035317 | 0.0030903 | 0.0027469 | 0.0024722 | 0.0022475 | 0.0020602 | 0.0019017 | 0.0017659 | 0.0016481 | 0.0015451 | 0.0014542 | 0.0013735 | 0.0013012 | 0.0012361
9 | 0.0250000 | 0.0125000 | 0.0083333 | 0.0062500 | 0.0050000 | 0.0041667 | 0.0035714 | 0.0031250 | 0.0027778 | 0.0025000 | 0.0022727 | 0.0020833 | 0.0019231 | 0.0017857 | 0.0016667 | 0.0015625 | 0.0014706 | 0.0013889 | 0.0013158 | 0.0012500
9.1 | 0.0252778 | 0.0126389 | 0.0084259 | 0.0063194 | 0.0050556 | 0.0042130 | 0.0036111 | 0.0031597 | 0.0028086 | 0.0025278 | 0.0022980 | 0.0021065 | 0.0019444 | 0.0018056 | 0.0016852 | 0.0015799 | 0.0014869 | 0.0014043 | 0.0013304 | 0.0012639
9.2 | 0.0255556 | 0.0127778 | 0.0085185 | 0.0063889 | 0.0051111 | 0.0042593 | 0.0036508 | 0.0031944 | 0.0028395 | 0.0025556 | 0.0023232 | 0.0021296 | 0.0019658 | 0.0018254 | 0.0017037 | 0.0015972 | 0.0015033 | 0.0014198 | 0.0013450 | 0.0012778
9.3 | 0.0258333 | 0.0129167 | 0.0086111 | 0.0064583 | 0.0051667 | 0.0043056 | 0.0036905 | 0.0032292 | 0.0028704 | 0.0025833 | 0.0023485 | 0.0021528 | 0.0019872 | 0.0018452 | 0.0017222 | 0.0016146 | 0.0015196 | 0.0014352 | 0.0013596 | 0.0012917
9.4 | 0.0261111 | 0.0130556 | 0.0087037 | 0.0065278 | 0.0052222 | 0.0043519 | 0.0037302 | 0.0032639 | 0.0029012 | 0.0026111 | 0.0023737 | 0.0021759 | 0.0020085 | 0.0018651 | 0.0017407 | 0.0016319 | 0.0015359 | 0.0014506 | 0.0013743 | 0.0013056
9.5 | 0.0263889 | 0.0131944 | 0.0087963 | 0.0065972 | 0.0052778 | 0.0043981 | 0.0037698 | 0.0032986 | 0.0029321 | 0.0026389 | 0.0023990 | 0.0021991 | 0.0020299 | 0.0018849 | 0.0017593 | 0.0016493 | 0.0015523 | 0.0014660 | 0.0013889 | 0.0013194
9.6 | 0.0266667 | 0.0133333 | 0.0088889 | 0.0066667 | 0.0053333 | 0.0044444 | 0.0038095 | 0.0033333 | 0.0029630 | 0.0026667 | 0.0024242 | 0.0022222 | 0.0020513 | 0.0019048 | 0.0017778 | 0.0016667 | 0.0015686 | 0.0014815 | 0.0014035 | 0.0013333
9.7 | 0.0269444 | 0.0134722 | 0.0089815 | 0.0067361 | 0.0053889 | 0.0044907 | 0.0038492 | 0.0033681 | 0.0029938 | 0.0026944 | 0.0024495 | 0.0022454 | 0.0020726 | 0.0019246 | 0.0017963 | 0.0016840 | 0.0015850 | 0.0014969 | 0.0014181 | 0.0013472
9.8 | 0.0272222 | 0.0136111 | 0.0090741 | 0.0068056 | 0.0054444 | 0.0045370 | 0.0038889 | 0.0034028 | 0.0030247 | 0.0027222 | 0.0024747 | 0.0022685 | 0.0020940 | 0.0019444 | 0.0018148 | 0.0017014 | 0.0016013 | 0.0015123 | 0.0014327 | 0.0013611
9.9 | 0.0275000 | 0.0137500 | 0.0091667 | 0.0068750 | 0.0055000 | 0.0045833 | 0.0039286 | 0.0034375 | 0.0030556 | 0.0027500 | 0.0025000 | 0.0022917 | 0.0021154 | 0.0019643 | 0.0018333 | 0.0017188 | 0.0016176 | 0.0015278 | 0.0014474 | 0.0013750
10 | 0.0277778 | 0.0138889 | 0.0092593 | 0.0069444 | 0.0055556 | 0.0046296 | 0.0039683 | 0.0034722 | 0.0030864 | 0.0027778 | 0.0025253 | 0.0023148 | 0.0021368 | 0.0019841 | 0.0018519 | 0.0017361 | 0.0016340 | 0.0015432 | 0.0014620 | 0.0013889
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

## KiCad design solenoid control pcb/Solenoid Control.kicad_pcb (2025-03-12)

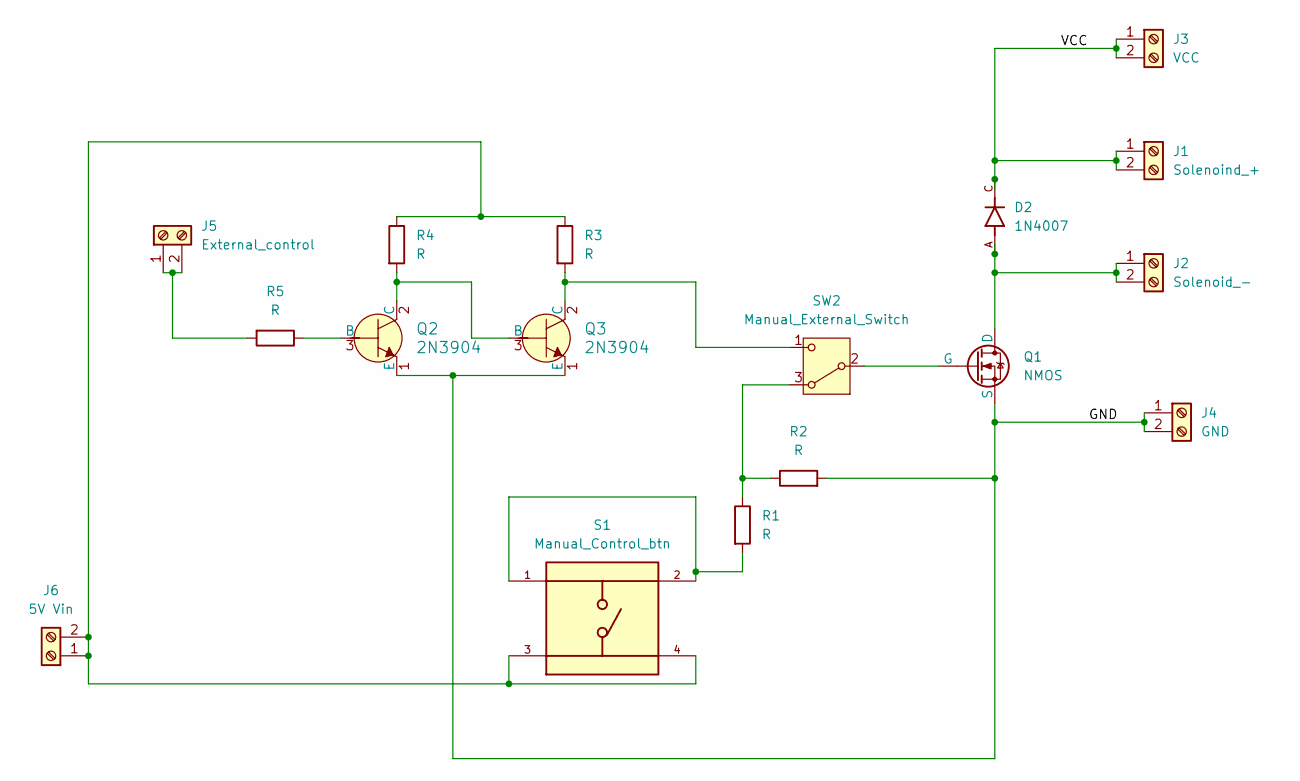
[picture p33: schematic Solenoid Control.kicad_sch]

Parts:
D2: 1N4007; DIOAD1060W80L520D270; PARTREV G
J1: Solenoind_+; TerminalBlock_TE_282834-2_1x02_P2.54mm_Horizontal
J2: Solenoid_-; TerminalBlock_TE_282834-2_1x02_P2.54mm_Horizontal
J3: VCC; TerminalBlock_TE_282834-2_1x02_P2.54mm_Horizontal
J4: GND; TerminalBlock_TE_282834-2_1x02_P2.54mm_Horizontal
J5: External_control; TerminalBlock_TE_282834-2_1x02_P2.54mm_Horizontal
J6: 5V Vin; TerminalBlock_TE_282834-2_1x02_P2.54mm_Horizontal
Q1: NMOS; TO254P1024X444X1989-3
Q2, Q3: 2N3904; TO-92L; MPN 2N3904
R1, R2, R3, R4, R5: R; R_Axial_DIN0207_L6.3mm_D2.5mm_P10.16mm_Horizontal
S1: Manual_Control_btn; SW_TS02-66-50-BK-160-LCR-D; PARTREV 1.0
SW2: Manual_External_Switch; SW_Slide-03_Wuerth-WS-SLTV_10x2.5x6.4_P2.54mm

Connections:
/GND: J4.1, J4.2, Q1.3 (S), Q2.1 (E), Q3.1 (E), R2.2
/VCC: D2.C, J1.1, J1.2, J3.1, J3.2
unnamed: D2.A, J2.1, J2.2, Q1.1 (D)
unnamed: J5.1, J5.2, R5.2
unnamed: J6.1, J6.2, R3.1, R4.1, S1.3, S1.4
unnamed 5: Q1.2 (G), SW2.2 (B); also elsewhere on the board
unnamed: Q2.3 (B), R5.1
unnamed: Q2.2 (C), Q3.3 (B), R4.2
unnamed 8: Q3.2 (C), R3.2, SW2.1 (C); also elsewhere on the board
unnamed: R1.2, S1.1, S1.2
unnamed 10: R1.1, R2.1, SW2.3 (A); also elsewhere on the board

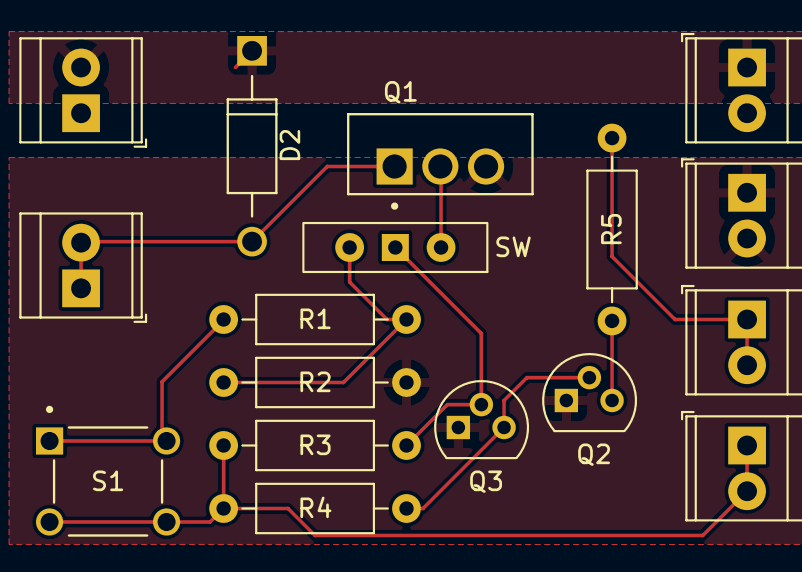
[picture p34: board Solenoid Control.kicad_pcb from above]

Board: 2 copper layers, 17 parts (0 on the bottom side), 11 nets.

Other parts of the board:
SW: Manual_External_Switch; SW_Slide-03_Wuerth-WS-SLTV_10x2.5x6.4_P2.54mm

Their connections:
unnamed 5: SW.2 (B); also elsewhere on the board
unnamed 8: SW.1 (C); also elsewhere on the board
unnamed 10: SW.3 (A); also elsewhere on the board

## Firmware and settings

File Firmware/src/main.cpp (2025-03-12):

#include <Arduino.h>

// Pin assignments (adjust as needed)
/*
  INPUT A - WHITE - DIRECTION
  INPUT B - BLACK - STEP
  ENABLE  - BLUE -
*/
#define STEP 11    // PWM-capable pin for step signal - BLACK - 11
#define DIR  10    // Simple digital pin for direction - WHITE - 10
#define ENABLE 9 // Enabled high - BLUE - 9
#define TRIGGER 5 // Green
#define AZI_MOVE_DONE 2
#define LED LED_BUILTIN

// Control parameters
#define AZI_DELAY 100
#define TRIGGERING_DELAY 75

int i;
volatile int receivedNumber = 0;  // Global variable for the received number
volatile int direction = 0;
char inputBuffer[6];              // Buffer to store incoming number (-800 to 800, max 5 chars + null)

unsigned long previousMillis = 0; // Stores the last time the action was performed
const unsigned long interval = 100; // Interval (0.1 second)

void stepMotor(unsigned long steps, 
                     bool direction)
{
  // Set the direction pin
  digitalWrite(DIR, direction ? HIGH : LOW);

  for (int i = 0; i < steps; i++)
  //while(true)
  {
    digitalWrite(STEP, HIGH);
    delayMicroseconds(AZI_DELAY);
    digitalWrite(STEP, LOW);
    delayMicroseconds(AZI_DELAY);
  }
  //digitalWrite(LED, LOW);
  //digitalWrite(ENABLE, LOW);
}

void move_done()
{

  Serial.write("1");
  
}

void setup()
{
  Serial.begin(115200);  // High baud rate for fast transmission

  // Set up the direction pin
  pinMode(DIR, OUTPUT);
  pinMode(STEP, OUTPUT);
  pinMode(ENABLE, OUTPUT);
  pinMode(LED, OUTPUT);
  pinMode(TRIGGER, OUTPUT);
  pinMode(AZI_MOVE_DONE, INPUT_PULLUP);

  digitalWrite(ENABLE, HIGH);
  digitalWrite(LED, HIGH);
  digitalWrite(STEP, LOW);
  //stepMotor(400,true);
  attachInterrupt(digitalPinToInterrupt(AZI_MOVE_DONE), move_done, FALLING);

}

void loop()
{
  digitalWrite(TRIGGER, LOW);
  unsigned long currentMillis = millis(); // Get the current time
  while (Serial.available()) {
      char c = Serial.read();  // Read a character
      Serial.write(c);

      if (c == '\n') {  // End of input, process the number
        inputBuffer[i] = '\0';  // Null-terminate the string
          int num = atoi(inputBuffer);  // Convert to integer
          // Movement Command
          if (num >= -800 && num <= 800) {  // Validate range
              receivedNumber = abs(num);  // Update global variable
              if (num > 0)
              {
                direction = 0;
              }
              else 
              {
                direction = 1;
              }
              digitalWrite(LED, HIGH);
              stepMotor(receivedNumber, direction);
          }

          i = 0;  // Reset index for next input
          
      } 
      else if (c == 'd' || c == 'D')
      {
        digitalWrite(ENABLE, LOW);
      }
      else if (c == 'e' || c == 'E')
      {
        digitalWrite(ENABLE, HIGH);
      }
      else if (c == 't' || c == 'T')
      {
        digitalWrite(TRIGGER, HIGH);
        delay(TRIGGERING_DELAY);
        digitalWrite(TRIGGER, LOW);
      }
      else if (i < sizeof(inputBuffer) - 1) {  // Store character if within buffer size
        inputBuffer[i] = c;
        i++;
      }
  }

  // 0.1 second interrupt
  if (currentMillis - previousMillis >= interval) 
  {
    previousMillis = currentMillis; // Update the last action time

  }
}

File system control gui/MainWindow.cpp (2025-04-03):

#include "CameraCaptureThread.h"
#include "MainWindow.h"
#include <QtCore/QDebug>
#include <QtCore/QDir>
#include <QtCore/QFileInfo>
#include <QtCore/QFileInfoList>
#include <QtCore/QStringList>
#include <QtWidgets/QMessageBox>
#include <QtWidgets/QFileDialog>
#include <QtCore/QStandardPaths>
#include <QtCore/QFile>
#include "CameraStreamWidget.h"
#include "CameraCalibration.h"
#include "AltitudeControl.h"
#include "AzimuthControl.h"
#include <chrono>
#include <thread>
#include <gl/GL.h>
#include "json.hpp"
#include <fstream>
#include <QSerialPort>
#include "ImageProcessing.h"
#include <QtConcurrent>
#include <QFuture>
#include <QMutex>
#include <time.h>
#include <sstream>
#include <cmath>
#include <iomanip>
#include <Eigen/Core>
#include <Eigen/Dense>
#include <unsupported/Eigen/LevenbergMarquardt>
#include <vector>
#include <cmath>
#include "YOLOInferenceWorker.h"
#include <QSerialPortInfo>
//#include <QmlDebuggingEnabler>

using json = nlohmann::json;

//QQmlDebuggingEnabler enabler;

MainWindow::MainWindow(QWidget *parent): QMainWindow(parent), captureThread(nullptr), serialPort(new QSerialPort(this)) {
    ui.setupUi(this);  // Sets up the UI and initializes the widgets
    qDebug()<<"setup ui";
    this->adjustSize();
    // showMaximized();





    connect(ui.selectCal3DFromSavedFile, &QRadioButton::toggled, this, &MainWindow::toggleCal3DType);
    connect(ui.selectNewCal3D, &QRadioButton::toggled, this, &MainWindow::toggleCal3DType);

    connect(ui.selectMoCamCalFromSavedFile, &QRadioButton::toggled, this, &MainWindow::toggleMotorCameraCalType);
    connect(ui.selectNewMoCamCal, &QRadioButton::toggled, this, &MainWindow::toggleMotorCameraCalType);

    connect(ui.savedCal3DFilesRefreshButton, &QPushButton::clicked, this, &MainWindow::updateSavedCameraCalibrationFilesComboBox);
    connect(ui.savedMoCamFilesRefreshButton, &QPushButton::clicked, this, &MainWindow::updateSavedMotorCameraCalibrationFilesComboBox);


    connect(ui.calibrateCal3DFromLoadedFile, &QPushButton::clicked, this, &MainWindow::calibrateCameraWithSelectedFile);
    connect(ui.calibrateMoCamFromLoadedFile, &QPushButton::clicked, this, &MainWindow::calibrateMotorCameraWithSelectedFile);


    connect(ui.newCal3DStartImageCaptureButton, &QPushButton::clicked, this, &MainWindow::newCameraCalibrationStartImageCapture);
    connect(ui.newCal3DSaveImagePairButton, &QPushButton::clicked, this, &MainWindow::newCameraCalibrationSaveImagePair);
    connect(ui.newCal3DStopImageCaptureButton, &QPushButton::clicked, this, &MainWindow::newCal3DStopImageCapture);
    // connect(ui.cancelNewCal3DButton, &QPushButton::clicked, this, &MainWindow::cancelNewCal3D);
    connect(ui.calibrateNewCal3DButton, &QPushButton::clicked, this, &MainWindow::calibrateCameras);
    connect(ui.startCameraCaptureThreadButton, &QPushButton::clicked, this, &MainWindow::startCapture);
    connect(ui.stopCameraCaptureThreadButton, &QPushButton::clicked, this, &MainWindow::stopCapture);
    //connect(ui.startMotorCameraCalibrationButton, &QPushButton::clicked, this, &MainWindow::calibrateMotorCamera);
    connect(ui.sendMotorPositionButton, &QPushButton::clicked, this, &MainWindow::sendMotorPositions);
    connect(ui.setProcessingButton, &QPushButton::clicked, this, &MainWindow::setProcesseing);
    connect(ui.calibrateSphericalButton, &QPushButton::clicked, this, &MainWindow::sphericalCalibration);
    connect(ui.targetAimButton, &QPushButton::clicked, this, &MainWindow::sphericalTest);
    connect(ui.setBackgroundImageButton, &QPushButton::clicked, this, &MainWindow::setBackgroundImage);

    connect(ui.fireButton, &QPushButton::clicked, this, &MainWindow::fire);


    connect(ui.initAlPushButton, &QPushButton::clicked, this, &MainWindow::initializeAltitude);
    connect(ui.initAzPushButton, &QPushButton::clicked, this, &MainWindow::initializeAzimuth);
    connect(ui.enableAzButton, &QPushButton::clicked, this, &MainWindow::enableAzimuth);
    connect(ui.disableAzButton, &QPushButton::clicked, this, &MainWindow::disableAzimuth);

    connect(ui.testMoveTimeButton, &QPushButton::clicked, this, &MainWindow::altitudeTimeTest);



    connect(ui.sendAltitudeButton, &QPushButton::clicked, this, &MainWindow::altitudeTest);
    connect(ui.sendAzimuthButton, &QPushButton::clicked, this, &MainWindow::azimuthTest);
    connect(this, &MainWindow::processedFramesReady, this, &MainWindow::onProcessedFramesReady);
    connect(ui.takePictureButton, &QPushButton::clicked, this, &MainWindow::saveProcessedFrames);

    connect(ui.enableAlButton, &QPushButton::clicked, this, &MainWindow::enableAltitude);
    connect(ui.disableAlButton, &QPushButton::clicked, this, &MainWindow::disableAltitude);

    connect(ui.goToAlLimitButton, &QPushButton::clicked, this, &MainWindow::moveAlLimit);
    connect(ui.goToAzLimitButton, &QPushButton::clicked, this, &MainWindow::moveAzLimit);

    connect(ui.setLowerAzLimit, &QPushButton::clicked, this, &MainWindow::setAzimuthLowerLimit);
    connect(ui.setUpperAzLimit, &QPushButton::clicked, this, &MainWindow::setAzimuthUpperLimit);
    connect(ui.setLowerAlLimit, &QPushButton::clicked, this, &MainWindow::setAltitudeLowerLimit);
    connect(ui.setUpperAlLimit, &QPushButton::clicked, this, &MainWindow::setAltitudeUpperLimit);

    connect(ui.startMotorCameraCalibrationButton, &QPushButton::clicked, this, &MainWindow::sweepLookupTable);

    connect(ui.farSweepRadioButton, &QRadioButton::toggled, this, &MainWindow::toggleNearFarSweep);
    connect(ui.nearSweepRadioButton, &QRadioButton::toggled, this, &MainWindow::toggleNearFarSweep);


    connect(ui.calculateLookupTableButton, &QPushButton::clicked, this, &MainWindow::getLookupTable);

    connect(ui.numPointsAzimuthSpinbox, QOverload<int>::of(&QSpinBox::valueChanged),
            [this](int newValue) {
                ui.numAzInterpPointsSpinBox->setMinimum(newValue);
            });

    connect(ui.numPointsAltitudeSpinbox, QOverload<int>::of(&QSpinBox::valueChanged),
            [this](int newValue) {
                ui.numAlInterpPointsSpinBox->setMinimum(newValue);
            });


    connect(ui.aimButton, &QPushButton::clicked, this, &MainWindow::aimAtCentroid);
    connect(ui.mcAimButton, &QPushButton::clicked, this, &MainWindow::aimAtCentroid);
    //connect(ui.startContinuousAimButton, &QPushButton::clicked, this, &MainWindow::aimContinuous);
    //connect(ui.stopContinuousAimButton, &QPushButton::clicked, this, &MainWindow::stopContinuousAim);

    connect(ui.startCentroidPushButton, &QPushButton::clicked, this, &MainWindow::toggleCaptureCentroid);
    connect(ui.saveCentroidPushButton, &QPushButton::clicked, this, &MainWindow::saveCentroidListToJson);

    connect(ui.startPredictionPushButton, &QPushButton::clicked, this, &MainWindow::togglePrediction);

    connect(this, &MainWindow::predictionDataReady, this, &MainWindow::runPrediction);



    qDebug()<<"connected thread";
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

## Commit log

2025-03-12 add electric design
    [Solenoid Control-B_Cu.gbr, Solenoid Control-B_Mask.gbr, Solenoid Control-B_Paste.gbr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]
2025-03-26 rename folder
    [Solenoid Control-B_Cu.gbr, Solenoid Control-B_Mask.gbr, Solenoid Control-B_Paste.gbr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]
2025-03-27 altitude motor stuff
2025-03-29 motor stuff
2025-03-31 camera stuff
2025-04-01 camera parameters
    [Camera Calculations.xlsx]
2025-04-01 camera paramete talbe
2025-04-01 some camera stuff
2025-04-02 yap motor tuning
2025-04-03 add calibration data
2025-04-16 added to launcher-camera calibration section
